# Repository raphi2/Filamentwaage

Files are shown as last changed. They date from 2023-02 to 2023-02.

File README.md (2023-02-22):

# Filamentwaage

Konzept und Umsetzung: Bader Raphael, Brockschmidt Sophia, Moser Anna

### Kurzübersicht

[Link zum Grafana Dashboard](http://217.160.37.170:3000/d/aa0QPgJ4z/wagezelle-ender-3-pro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)

Lokale Webseite der Waage aufrufbar unter: [10.0.8.146](http://10.0.8.146)

### Zielstellung

Winterchallenge Studiengang Smart Products and Solutions 2022:

Aufgabenstellung: Einbindung der 3D-Filament Drucker im Makers Lab der FH in eine digital factory

Ziele: 
- Vernetzung und Möglichkeit des Remote Betriebs
- Predictive Maintenance durch geeignete Geräteüberwachung, in diesem Fall des Rohstoffs
- Überwachung des verbleibenden Filaments

### Verwendete Hardware: 

- Microcontoller: ESP32 Vroom
- Sensor: Wägezelle 5kg ([Amazon Link](https://www.amazon.de/dp/B073GWX6J4?ref=ppx_yo2ov_dt_b_product_details&th=1))
- A/D Wandler: HX711
- Schrauben: 2x M5x20mm / 2x M4x20mm
- diverse Jumperkabel
- Steckboard
- additiv gefertigte Halterung für Wägezelle

### Verwendete Bibliotheken:
- HX711  
- ESPAsyncWebServer 
- AsyncElegantOTA
- ESP8266 Influxdb

### Pinbelegung ESP32

- GPIO 33 = DT data 
- GPIO 32 = SCK clock

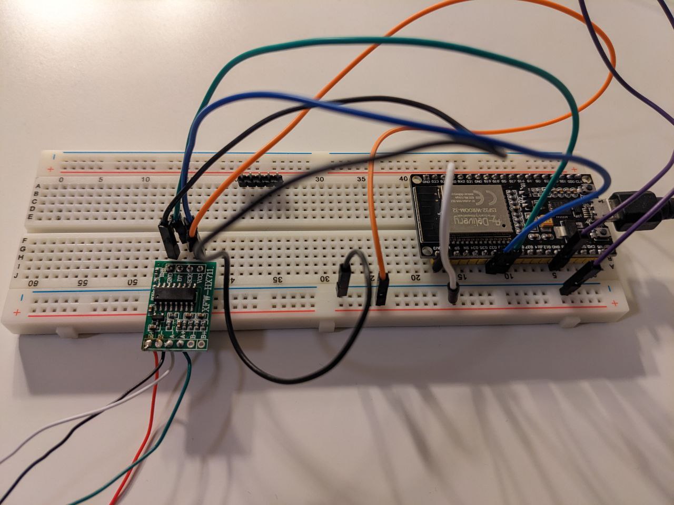
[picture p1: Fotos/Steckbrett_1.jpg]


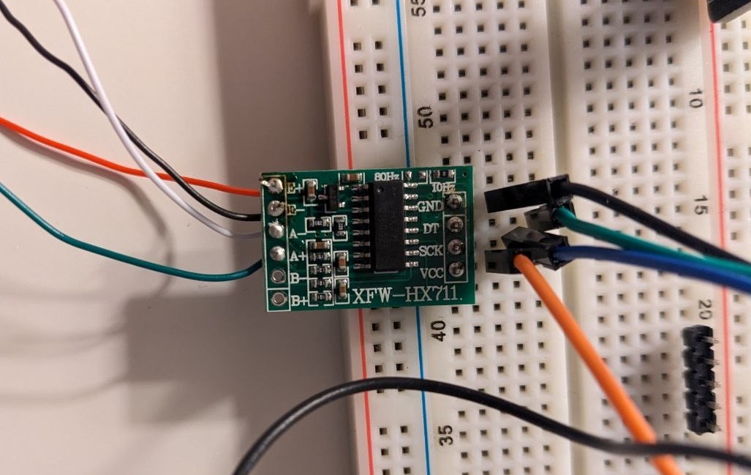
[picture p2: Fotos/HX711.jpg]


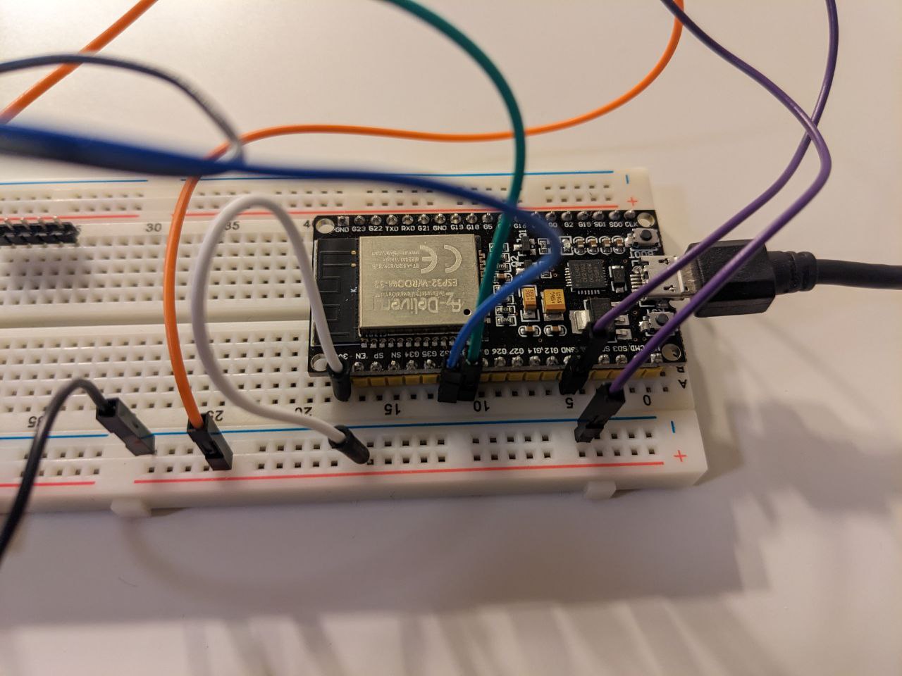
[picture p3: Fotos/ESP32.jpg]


### Kalibrierfaktor bestimmen
Für eine aussagekräftige Gewichtsangabe wurde zunächst der Kalibrierfaktor der Wägezelle mittels Normgewicht (100g) bestimmt. 
Kalibrierfaktor = angezeigter Wert 48466 / 100g 

-> der Kalibrierfaktor wurde im Programmcode ergänzt:

```scale.set_scale(48466/100);```

Um die Richtigkeit des Kalibrierungsfaktor zu überprüfen wurde anschließend das Normgewicht mit einer Präzisionswaage und der Wägezelle gemessen und der Wert miteinander verglichen. Der Unterschied zwischen den beiden Messungen war 0,05g.

### Web Server Anwendung

Folgende Website visualisiert das Filamentgewicht auf 0,01g genau und aktualisiert die Messung alle 5 Sekunden. 
Mittels Tara Button kann der aktuelle Gewichtswert tariert werden. Dies ist nur notwendig, wenn eine neue Filamentspule mit einer neuen Rolle verwendet wird. 
Desweiteren kann die Firmware des Microcontoller über Over-the-Air-Update aktualisiert werden: [10.0.8.146/update](http://10.0.8.146/update)

Screenshot der Webseite:
![alt text](https://github.com/raphi2/Filamentwaage/blob/master/Fotos/Website.JPG?raw=true)

### Halterung der Waage

Die Halterung der Waage wurde durch 3D Druck hergestellt und anschließend mit M5 und M4 Schrauben an der Wägezelle montiert.

([Link zu 3D Daten](3D))

Grün: Halterung / Orange: Auflage Spule
![alt text](https://github.com/raphi2/Filamentwaage/blob/master/Fotos/3D_Konzept.jpg?raw=true)

### Challenges

Folgende Challeges sind während der implemenation des Konzepts aufgetreten.

- Der Beispielcode des HX711 Wandlers enthält Befehle, welche den Microcontroller regelmäßig in den Sleep Mode versetzt, wodurch das Programm bei Einbindung des Webservers zum Absturz gebracht wird.
- Die Lötstellen sind mehrfach ausgerissen
- Entfernen der Stützstruktur der additiv gefertigten Halterung
  - Mangelnde Genauigkeit der gedruckten Teile machten intensive Nacharbeit notwendig
- Gewichtszunahme am ruhenden Objekt durch Wärmeausdehnung: +0,9g nach 23min 28s

![alt text](https://github.com/raphi2/Filamentwaage/blob/master/Fotos/Gewichtszunahme_neu.JPG?raw=true)

Beim Probedruck eines ca. 1,5g schweren Deckels ist eine eine Zunahme des angezeigten Gewichtswerts sichtbar, wobei nach Ende des Drucks die Gewichtszunahme bei a. 4g war. Der Druck wurde um 18:08 gestartet und endete um 18:28.
![alt text](https://github.com/raphi2/Filamentwaage/blob/master/Fotos/Druckversuch.JPG?raw=true)

Mögliche Ursachen für die Zunahme sind:
- Aufgrund des Filamentvorschubs am 3D Drucker entstehen Zugkraft an der Filamentspule 
  - mögliche Lösung: andere Zuführung des Filaments, ggf Umlenkung vorsehen
- Die Filamentspule ist unwucht, wodurch die großen Sprünge bei der Messung entstehen
- Zu geringe Gewichtsabnahme des Filaments für eine aussagekräftige Messung

### Fazit

Theoretisch ist die Filamentwaage in der Lage auf 0,01g genau zu gemessen. In der Praxis sind Schwankungen bei ruhiggelagerten Objekten von mind. 0,2g zu beobachten. Für die oben beschriebene Anwendung ist dies jedoch vernachlässigbar.

Im folgenden Graph sind zwei Linien zu erkennen: 
Die grüne Linie visualisiert eine Messung, die gelbe Linie den Mittelwert aus 10 Messungen darstellt. Durch die Berechnung des Mittelwertes können große Messabweichungen eleminiert und die Messkurve geglättet werden.

![alt text](https://github.com/raphi2/Filamentwaage/blob/master/Fotos/Mittelwert_neu.JPG?raw=true)

Um eine aussagekräftige Gewichtsmessung zu erhalten, muss die Wägezelle vor Inbetriebnahme auf Raumtemperatur gebracht werden. 

Für ein finales Ergebnis des Projekts muss noch eine Langzeitmessung während eines längeren Drucks gemacht werden. Nur dann kann die Korrektheit der Messung während des Betriebs überprüft, bzw. korrigiert werden.

Aufbau der Filamentwaage am Ender 3 Pro.
![Aufbau am Ender 3 Pro](https://github.com/raphi2/Filamentwaage/blob/master/Fotos/Foto_1.jpg?raw=true)

#### Mögliche Verbesserungen

- andere Zuführung bzw. Umlenkung des Filaments zur Reduktion der Zugkräfte
- widerstandsarme Lagerung der Filamentspule, durch bspw. Kugellager
- Integration eines Graphen auf der Webseite zur Darstellung des Gewichts über eine bestimmte Zeitperiode
- Algorithmus implementieren, der die Messabweichungen während des Drucks kompensiert
- Algorithmus implementieren, der den nächsten Wechsel der Filamentspule voraussagt
- Anpassung des Messintervalls an Spulenverbrauch

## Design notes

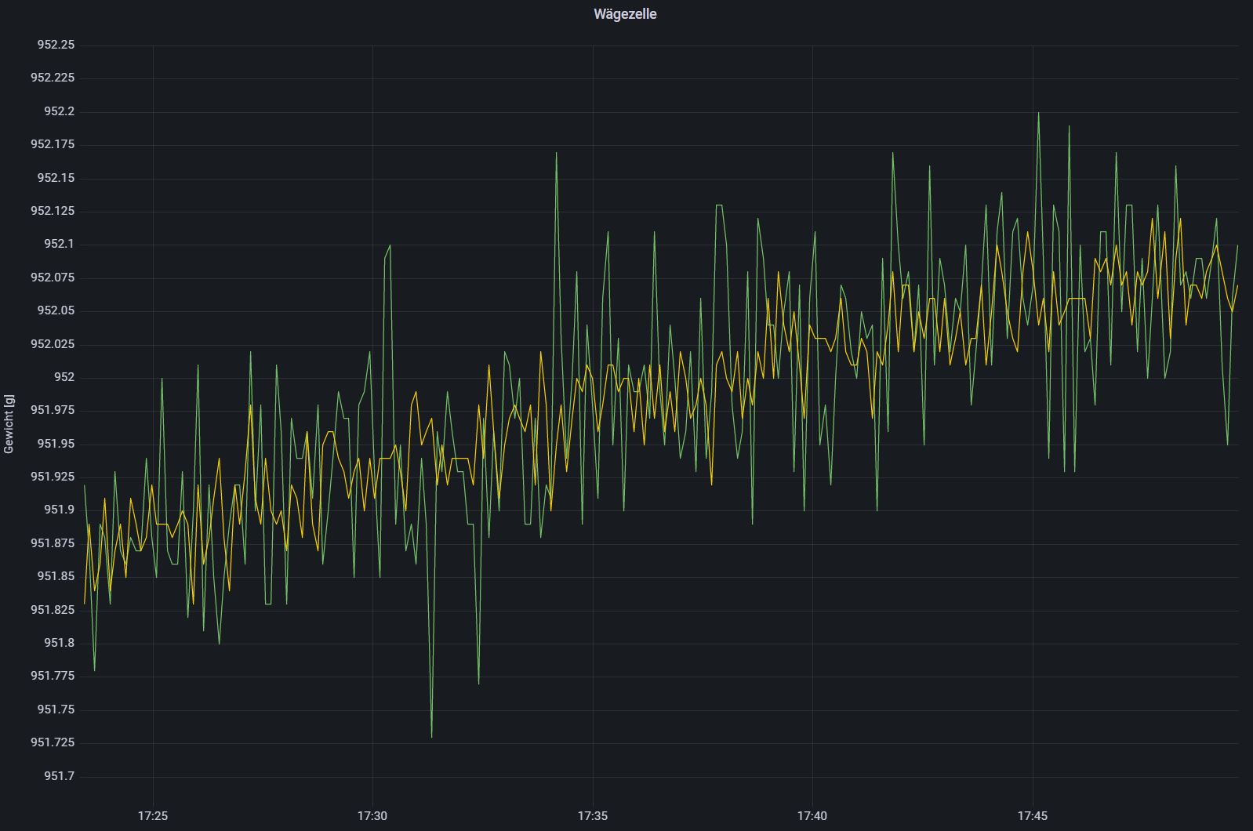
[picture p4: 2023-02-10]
Fotos/Mittelwert_neu.JPG

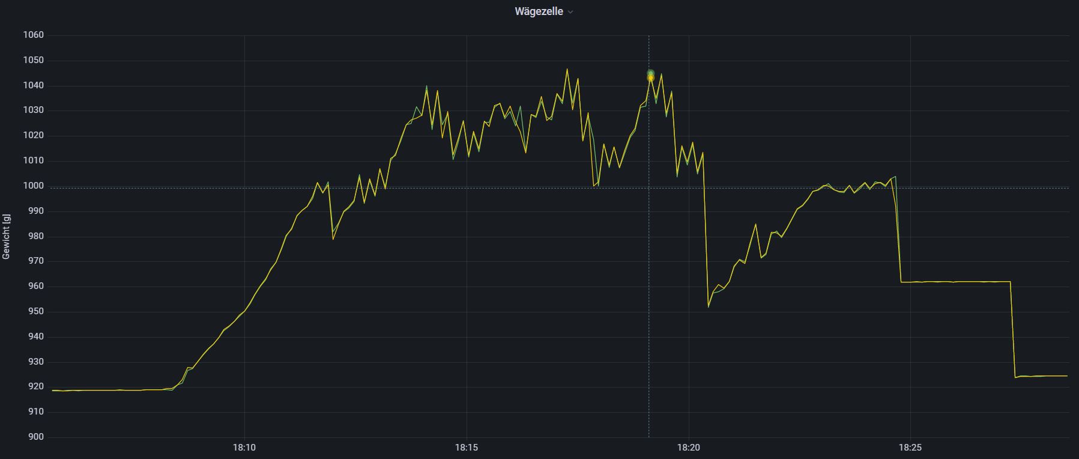
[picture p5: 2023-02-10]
Fotos/Druckversuch.JPG

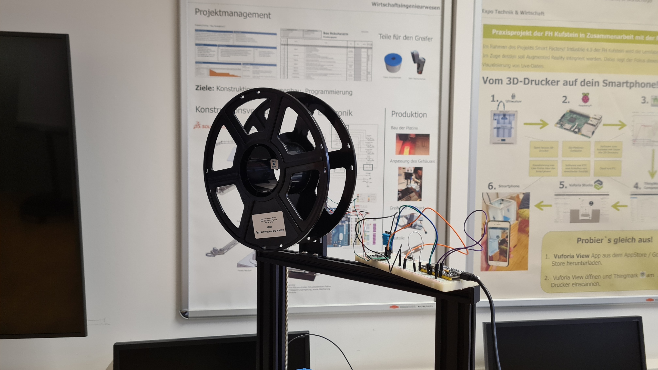
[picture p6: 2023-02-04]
Fotos/Foto2.jpg

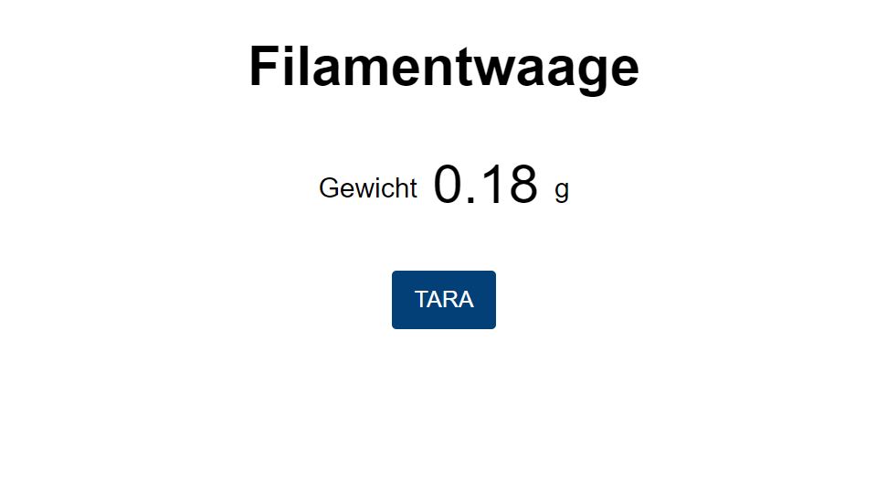
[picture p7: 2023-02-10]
Fotos/Website.JPG

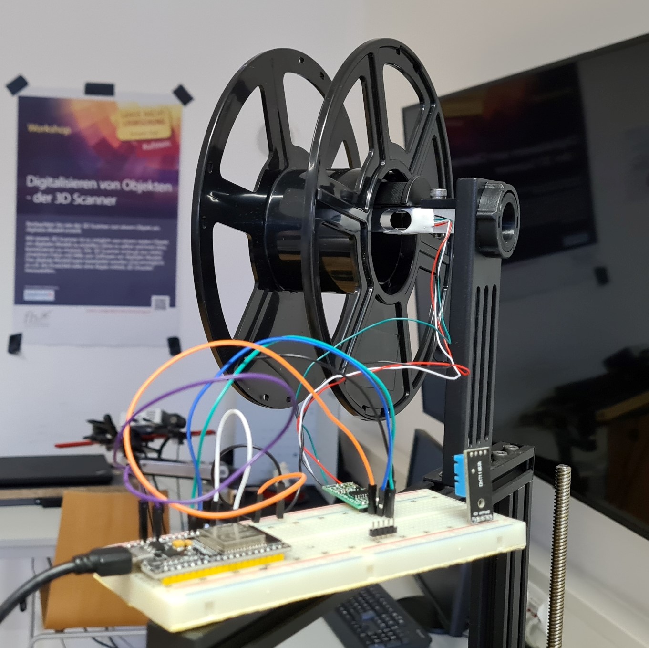
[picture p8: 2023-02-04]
Fotos/Foto_1.jpg

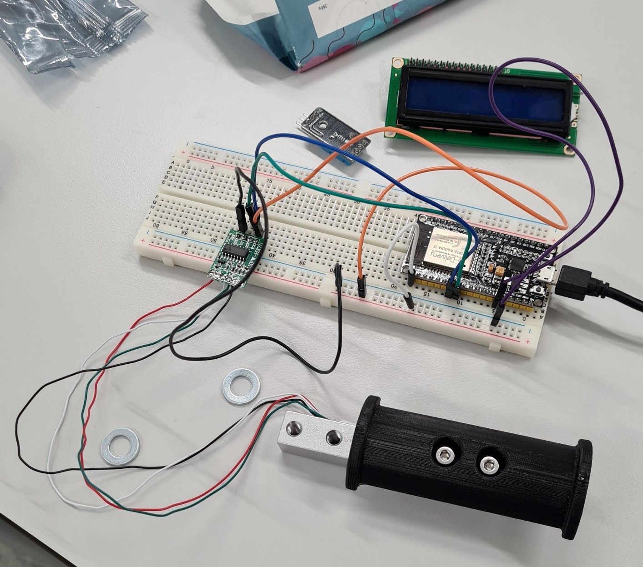
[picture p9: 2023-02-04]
Fotos/Steckbrett.jpg

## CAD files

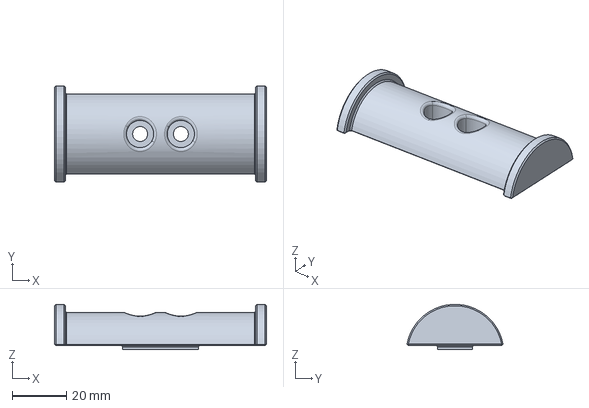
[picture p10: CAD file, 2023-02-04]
3D/STP/Auflage Spule.stp
78.0 x 35.4 x 16.6 mm

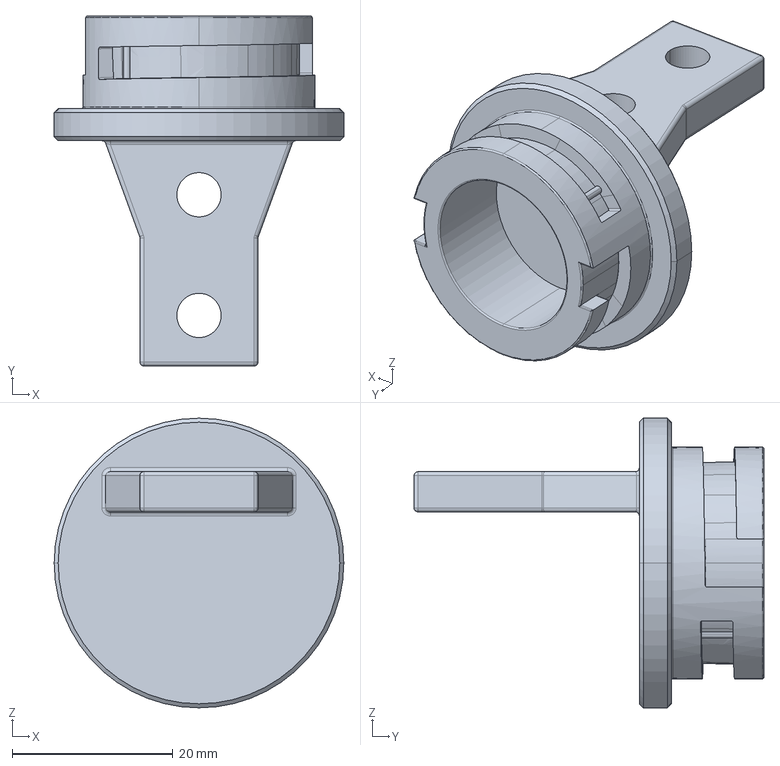
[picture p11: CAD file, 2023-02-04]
3D/STP/Halterung.stp
36.0 x 43.5 x 36.0 mm

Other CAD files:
3D/Catia/Auflage Spule.CATPart
3D/Catia/Ender 3 Filament Halter.CATProduct
3D/Catia/Halterung.CATPart
3D/Catia/ISO_4762_M4x20_STEEL_HEXAGON_SOCKET_HEAD_CAP_SCREW.CATPart
3D/Catia/ISO_4762_M5x20_STEEL_HEXAGON_SOCKET_HEAD_CAP_SCREW.CATPart
3D/Catia/Mutter_Halter.CATPart
3D/Catia/Original_Halterung.CATPart
3D/Catia/Spool_Holder_Ender3_1.CATPart
3D/Catia/Teil1.CATPart
3D/Catia/Zelle.CATPart
3D/STL/Auflage Spule.stl
3D/STL/Halterung.stl

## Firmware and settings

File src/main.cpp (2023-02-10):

/**
Filamentwaage für 3D Drucker
Idee und Umsetzung: Bader Raphael, Brockschmidt Sophia, Moser Anna
Wurde im Zuge der SPS Winterchallenge 2022/23 an der FH Kufstein erarbeitet
**/

//import of libraries
#include <Arduino.h>
#include <HX711.h>
#include <WiFi.h>
#include <ESPAsyncWebServer.h>
#include <AsyncElegantOTA.h>
#include <AsyncTCP.h>

//InfluxDB library and definitions
#define DEVICE "ESP32"
#include <WiFiMulti.h>
WiFiMulti wifiMulti;
#include <InfluxDbClient.h>

// HX711 circuit wiring
const int LOADCELL_DOUT_PIN = 33;
const int LOADCELL_SCK_PIN = 32;

// Replace with your network credentials
const char* ssid = "FH_MEDIEN";
const char* password = "P##96bCqXYuuF*e";

// InfluxDB URL
#define INFLUXDB_URL "http://217.160.37.170:8086"
// InfluxDB Name
#define INFLUXDB_DB_NAME "dbSPS22"
InfluxDBClient client(INFLUXDB_URL, INFLUXDB_DB_NAME);

// Data point in InfluxDB
Point sensor("Wägezelle Ender 3 Pro");

// Set InfluxDB 1 authentication parameter
#define INFLUXDB_USER "SPS22"
#define INFLUXDB_PASSWORD "@home2learn"

// Create AsyncWebServer object on port 80
AsyncWebServer server(80);

//Definition of scale variable
HX711 scale;

// Code for HTML Webseite
const char index_html[] PROGMEM = R"rawliteral(
<!DOCTYPE HTML><html>
<head>
  <meta name="viewport" content="width=device-width, initial-scale=1">
  <link rel="stylesheet" href="https://use.fontawesome.com/releases/v5.7.2/css/all.css" integrity="sha384-fnmOCqbTlWIlj8LyTjo7mOUStjsKC4pOpQbqyi7RrhN7udi9RwhKkMHpvLbHG9Sr" crossorigin="anonymous">
  <style>
    html {
     font-family: Arial;
     display: inline-block;
     margin: 0px auto;
     text-align: center;
    }
    h2 { font-size: 3.0rem; }
    p { font-size: 3.0rem; }
    .units { font-size: 1.2rem; }
    .gewicht-labels{
      font-size: 1.5rem;
      vertical-align:middle;
      padding-bottom: 15px;
    }
    button {
      background-color: #034078;
      border: none;
      padding: 14px 20px;
      text-align: center;
      font-size: 20px;
      border-radius: 4px;
      transition-duration: 0.4s;
      color: white;
      cursor: pointer;
    }
    button:hover {
      background-color: #1282A2;
    }
  </style>
</head>

<body>
  <h2>Filamentwaage</h2>
  <p>
    <span class="gewicht-labels">Gewicht</span>
    <span id="gewicht">%GEWICHT%</span>
    <span class="gewicht-labels">g</span>
  </p>
  <button onclick="TaraScale()">TARA</button>


</body>
<script>

function TaraScale(){
  var xhr = new XMLHttpRequest();
  xhr.open("GET", "/button?value=", true);
  xhr.send();
}

setInterval(function ( ) {
  var xhttp = new XMLHttpRequest();
  xhttp.onreadystatechange = function() {
    if (this.readyState == 4 && this.status == 200) {
      document.getElementById("gewicht").innerHTML = this.responseText;
    }
  };
  xhttp.open("GET", "/gewicht", true);
  xhttp.send();
}, 10000 ) ;

</script>
</html>)rawliteral";

// Replaces placeholder with weight values
String processor(const String& var){
  //Serial.println(var);
  if(var == "GEWICHT"){
    return "Bitte warten";
  }
  return String();
}

void setup() {

  Serial.begin(115200);

  // InfluxDB connection
  // Connect WiFi - Influx DB
  Serial.println("Connecting to WiFi");
  WiFi.mode(WIFI_STA);
  wifiMulti.addAP(ssid, password);
  while (wifiMulti.run() != WL_CONNECTED) {
    Serial.print(".");
    delay(500);
  }
  Serial.println();

  // Set InfluxDB 1 authentication params
  client.setConnectionParamsV1(INFLUXDB_URL, INFLUXDB_DB_NAME, INFLUXDB_USER, INFLUXDB_PASSWORD);

  // Add constant tags - only once
  sensor.addTag("device", DEVICE);
  sensor.addTag("SSID", WiFi.SSID());

  // Check server connection
  if (client.validateConnection()) {
    Serial.print("Connected to InfluxDB: ");
    Serial.println(client.getServerUrl());
  } else {
    Serial.print("InfluxDB connection failed: ");
    Serial.println(client.getLastErrorMessage());
  }

  // Connect to Wi-Fi
  WiFi.begin(ssid, password);
  while (WiFi.status() != WL_CONNECTED) {
    delay(1000);
    Serial.println("Connecting to WiFi..");
  }

  // Print ESP32 Local IP Address
  Serial.println(WiFi.localIP());

  // Route for root / web page
  server.on("/", HTTP_GET, [](AsyncWebServerRequest *request){
    request->send_P(200, "text/html", index_html, processor);
  });
  server.on("/gewicht", HTTP_GET, [](AsyncWebServerRequest *request){
    request->send_P(200, "text/plain", String(scale.get_units()).c_str());
  });

  // Send a GET request to Tare Button - Scale Tare
  server.on("/button", HTTP_GET, [](AsyncWebServerRequest *request){
    scale.tare();               // reset the scale to 0
    });

  // Start server
  server.begin();

  WiFi.mode(WIFI_STA);
  WiFi.begin(ssid, password);
  Serial.println("");

  // Wait for connection
  while (WiFi.status() != WL_CONNECTED) {
    delay(500);
    Serial.print(".");
  }
  Serial.println("");
  Serial.print("Connected to ");
  Serial.println(ssid);
  Serial.print("IP address: ");
  Serial.println(WiFi.localIP());

  server.on("/", HTTP_GET, [](AsyncWebServerRequest *request) {
    request->send(200, "text/plain", "Hi! I am ESP32.");
  });

  AsyncElegantOTA.begin(&server);    // Start ElegantOTA
  server.begin();
  Serial.println("HTTP server started");

  Serial.println("Initializing the scale");

  scale.begin(LOADCELL_DOUT_PIN, LOADCELL_SCK_PIN);

  Serial.println("Before setting up the scale:");
  Serial.print("read: \t\t");
  Serial.println(scale.read());      // print a raw reading from the ADC

  Serial.print("read average: \t\t");
  Serial.println(scale.read_average(20));   // print the average of 20 readings from the ADC

  Serial.print("get value: \t\t");
  Serial.println(scale.get_value(5));   // print the average of 5 readings from the ADC minus the tare weight (not set yet)

  Serial.print("get units: \t\t");
  Serial.println(scale.get_units(5), 1);  // print the average of 5 readings from the ADC minus tare weight (not set) divided
            // by the SCALE parameter (not set yet)
           
  scale.set_scale(48466/100); // this value is obtained by calibrating the scale with known weights; see the README for details                  
  scale.tare();               // reset the scale to 0

  Serial.println("After setting up the scale:");

  Serial.print("read: \t\t");
  Serial.println(scale.read());                 // print a raw reading from the ADC

  Serial.print("read average: \t\t");
  Serial.println(scale.read_average(20));       // print the average of 20 readings from the ADC

  Serial.print("get value: \t\t");
  Serial.println(scale.get_value(5));   // print the average of 5 readings from the ADC minus the tare weight, set with tare()

  Serial.print("get units: \t\t");
  Serial.println(scale.get_units(5), 1);        // print the average of 5 readings from the ADC minus tare weight, divided
            // by the SCALE parameter set with set_scale

  Serial.println("Readings:");
}

void loop() {

  // Sensor data Output to console
  Serial.print("one reading:\t");
  Serial.print(scale.get_units(), 1);
  Serial.print("\t| average:\t");
  Serial.println(scale.get_units(10), 5);

  // Store measured value into point
  sensor.clearFields();
  sensor.addField("Gewicht", scale.get_units()); //store measurement of 1 reading into Database
  sensor.addField("Mittelwelt", scale.get_units(10)); //store the average of 10 readings into Database

  // Print what are we exactly writing
  Serial.print("Writing: ");
  Serial.println(client.pointToLineProtocol(sensor));

  // If no Wifi signal, try to reconnect it
  if (wifiMulti.run() != WL_CONNECTED) {
    Serial.println("Wifi connection lost");
  }
  // Write point
  if (!client.writePoint(sensor)) {
    Serial.print("InfluxDB write failed: ");
    Serial.println(client.getLastErrorMessage());
  }
  
  delay(5000);
}

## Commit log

2023-02-04 Fotos + 3D Daten
    [Auflage Spule.CATPart, Auflage Spule.stl, Auflage Spule.stp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]
2023-02-10 Tara Button + InfluxDB
2023-02-10 Tara Button
